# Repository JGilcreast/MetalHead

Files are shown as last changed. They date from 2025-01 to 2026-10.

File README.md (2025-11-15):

MetalHead

An opensource firmware and software drop-in replacement for the 85V Automatic Stirrup Bender by CRS Specialties Inc.
...short story behind the name...

# System Block Diagram
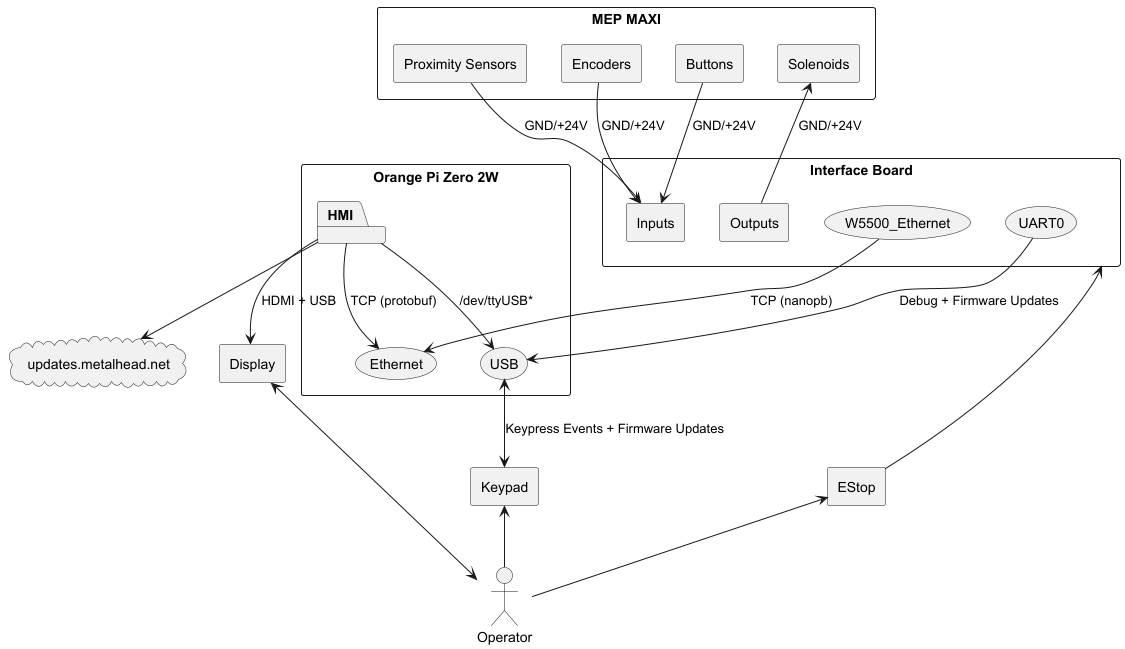
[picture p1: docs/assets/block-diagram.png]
Block Diagram


---

# Firmware
### HMI - Zephyr RTOS
* It's preferred to use CLion, 
* [Download](https://apps.microsoft.com/search?query=python&hl=en-US&gl=US) and install the latest version of python
* Install wget and 7Zip so that they're accessible via cmd:
  * `choco install wget 7zip`
* Verify python is accessible via cmd:
  * `python -V`
* Create python virtual environment
  * `cd MetalHead\firmware\interface-board-zephyr`
  * `python -m venv .\.venv`
* Enter python virtual environment
  * `.\.venv\Scripts\activate.bat`
* Update pip (optional)
  * `python.exe -m pip install --upgrade pip`
* Install west
  * `pip install west`
* Initiate the Zephyr-RTOS project
  * `west init`
* Set BOARD to rpi-pico
  * `west config zephyr.board rpi_pico`
* Pull the latest commits from Zephyr's github
  * `west update`
* Export a Zephyr CMake package. This allows CMake to automatically load boilerplate code required for building Zephyr applications.
  * `west zephyr-export`
  * > See: Computer\HKEY_CURRENT_USER\Software\Kitware\CMake\Packages
* Install additional packages need by west
  * `west packages pip --install`
* Install the Zephyr SDK
  * `west sdk install`
* Create a folder for bossac: C:\Program Files (x86)\BOSSA
* Copy bossac.exe to C:\Program Files (x86)\BOSSA
* Add C:\Program Files (x86)\BOSSA to PATH environment (use `sysdm.cpl`)
  * Make sure you can access bossac.exe. Open a new terminal and run: `bossac --help`
* Copy bossac.py from `MetalHead\firmware\interface-board-zephyr` to `MetalHead\firmware\interface-board-zephyr\zephyr\scripts\west_commands\runners`
* Start CLion
* Open our project: MetalHead\firmware\interface-board-zephyr\application
* Configure python interpreter for west
  * Go to File -> Settings -> Languages & Frameworks -> Python
  * Select the python interpreter from the list

To build a pristine copy of the firmware binary:[.gitignore](.gitignore)

  * `cd MetalHead\firmware\interface-board-zephyr`
  * `rmdir /q /s application\build`
  * Go back to CLion and reload West
  * Build, flash, etc

---

# Software
### HMI - Crude Edition
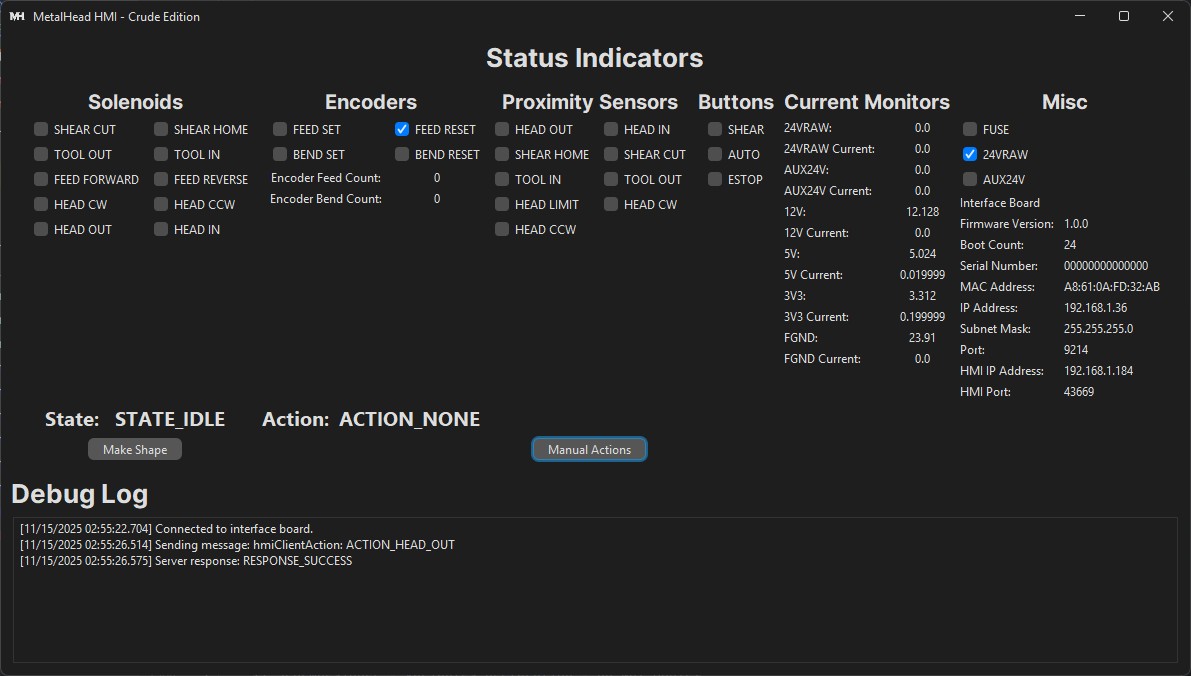
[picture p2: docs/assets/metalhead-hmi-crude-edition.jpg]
MetalHead HMI Crude Edition


This is a simple unpolished version of the HMI app that will eventually run on the orange pi.
This version is mostly for implementation and testing purposes.
### HMI
The polished version of the HMI app. This app version be able to accomplish the following:
* Must be able to communicate with the interface board bi-directionally
* Display all relevant information in realtime.
* Recognize user input from the custom keypad
* Offer simple 'wizards' that visually guide operators to make common shapes

Nice to have features:
* Auto-update HMI software by communicating to a remote server
* Auto-update interface firmware by communicating to a remote server
* Include a section for custom stirrup calculators/guides
* Include instructional videos on using the machinery

---

# Hardware
### Interface Board
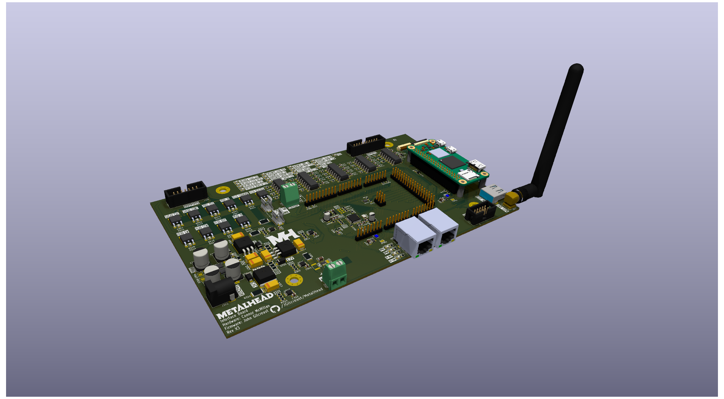
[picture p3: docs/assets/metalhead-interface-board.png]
MetalHead Interface Board


### Keypad
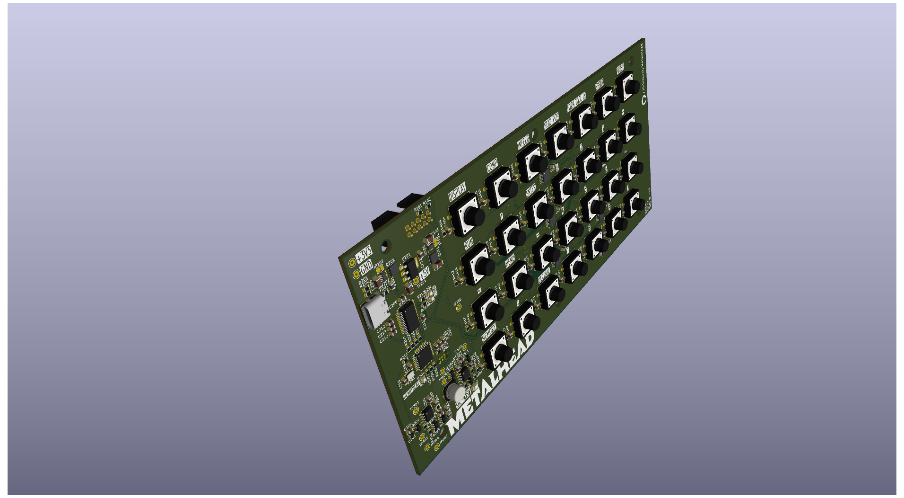
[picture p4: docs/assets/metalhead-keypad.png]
MetalHead Keypad


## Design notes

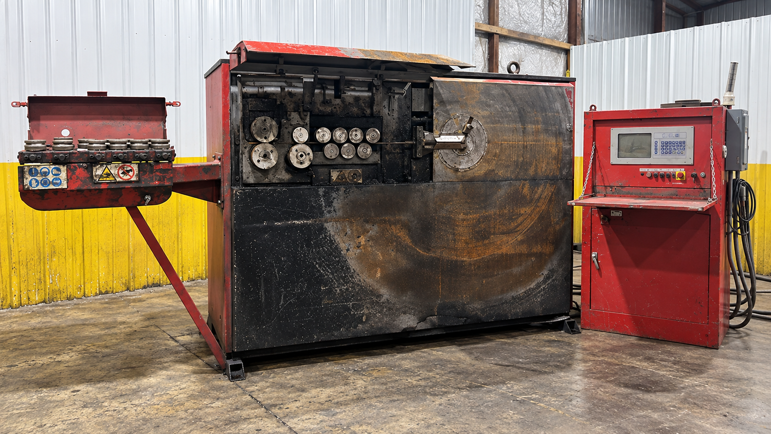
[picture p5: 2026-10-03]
docs/assets/CRS Specialties MEP MAXI 85V.png

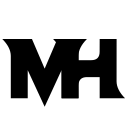
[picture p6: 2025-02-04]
docs/assets/MH-128.png

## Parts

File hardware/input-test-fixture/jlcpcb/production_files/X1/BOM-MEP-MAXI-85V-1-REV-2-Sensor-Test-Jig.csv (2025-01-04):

Comment | Designator | Footprint | LCSC | Quantity
Screw_Terminal_01x03 | J105 | TerminalBlock_TE_282834-3_1x03_P2.54mm_Horizontal |  | 1
Screw_Terminal_01x03 | J107 | TerminalBlock_TE_282834-3_1x03_P2.54mm_Horizontal |  | 1
Screw_Terminal_01x02 | J114 | TerminalBlock_TE_282834-2_1x02_P2.54mm_Horizontal |  | 1
Screw_Terminal_01x03 | J111 | TerminalBlock_TE_282834-3_1x03_P2.54mm_Horizontal |  | 1
Screw_Terminal_01x02 | J110 | TerminalBlock_TE_282834-2_1x02_P2.54mm_Horizontal |  | 1
Screw_Terminal_01x03 | J109 | TerminalBlock_TE_282834-3_1x03_P2.54mm_Horizontal |  | 1
Screw_Terminal_01x05 | J103 | TerminalBlock_TE_282834-5_1x05_P2.54mm_Horizontal |  | 1
Screw_Terminal_01x03 | J112 | TerminalBlock_TE_282834-3_1x03_P2.54mm_Horizontal |  | 1
Barrel_Jack_MountingPin | J115 | BarrelJack_Wuerth_6941xx301002 |  | 1
Conn_02x10_Odd_Even | J101 | IDC-Header_2x10_P2.54mm_Vertical |  | 1
Screw_Terminal_01x03 | J108 | TerminalBlock_TE_282834-3_1x03_P2.54mm_Horizontal |  | 1
Screw_Terminal_01x05 | J102 | TerminalBlock_TE_282834-5_1x05_P2.54mm_Horizontal |  | 1
Screw_Terminal_01x03 | J104 | TerminalBlock_TE_282834-3_1x03_P2.54mm_Horizontal |  | 1
Screw_Terminal_01x03 | J113 | TerminalBlock_TE_282834-3_1x03_P2.54mm_Horizontal |  | 1
Screw_Terminal_01x03 | J106 | TerminalBlock_TE_282834-3_1x03_P2.54mm_Horizontal |  | 1

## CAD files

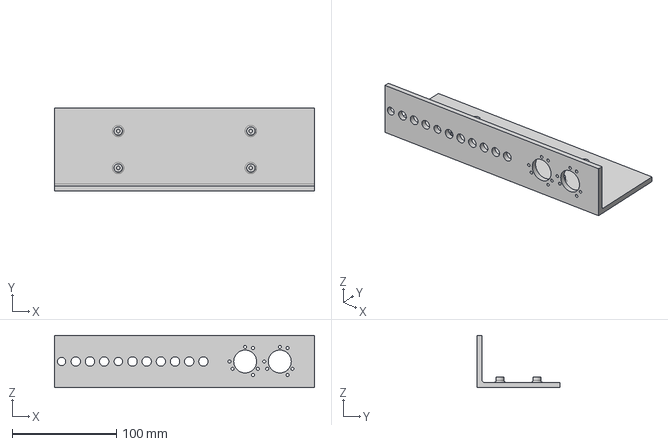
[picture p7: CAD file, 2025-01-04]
hardware/input-test-fixture/3D/X1/Input Test Fixture v3.step
250.0 x 80.0 x 50.0 mm

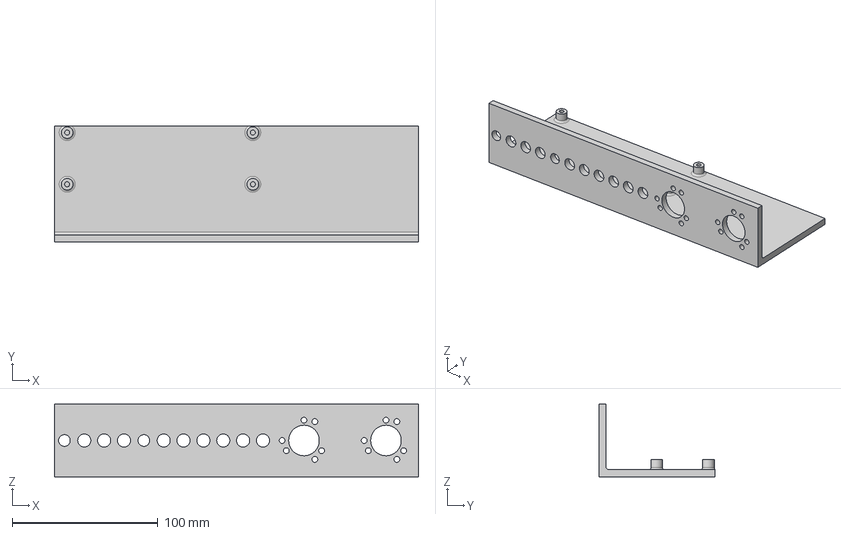
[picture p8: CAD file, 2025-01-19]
hardware/input-test-fixture/3D/X2/Input Test Fixture X2.step
250.0 x 80.0 x 50.0 mm

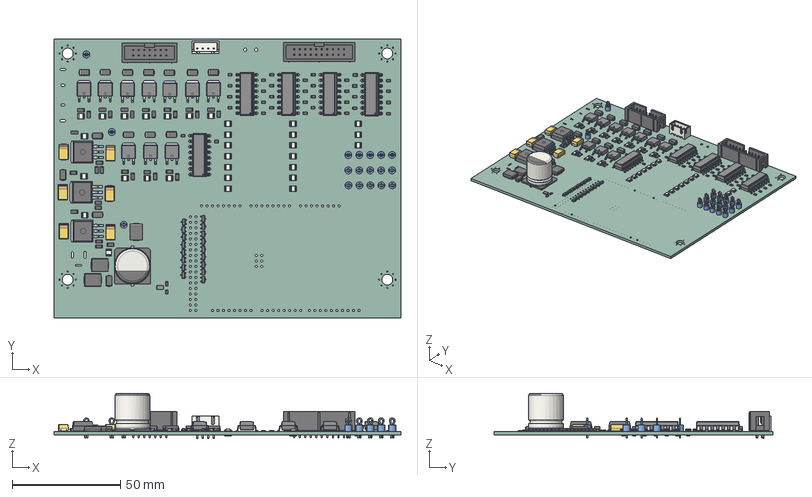
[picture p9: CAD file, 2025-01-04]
hardware/interface-board/production/X1/3D/MEP-MAXI-85V-1-REV-2-Interface-Board.step
160.0 x 128.5 x 20.9 mm
LED_1210_3225Metric x 31
D_SMA x 14
R_1206_3216Metric x 48
R_0805_2012Metric x 36
JST_B4B_XH_A
TestPoint_Loop_D2_60mm_Drill1_6mm_Beaded_cp x 18
SOT_23 x 17
IRFR7540TRPBF x 10
CP_EIA_7343_31_Kemet_D x 6
D_SMC x 3
LTV-846S x 5
CQ assembly x 3
CP_Elec_16x175
IDC_Header_2x10_P254mm_Vertical
ASSEMBLY
IDC_Header_2x07_P254mm_Vertical
_autosave-MEP-MAXI-85V-1-REV-2-Interface-Board_PCB

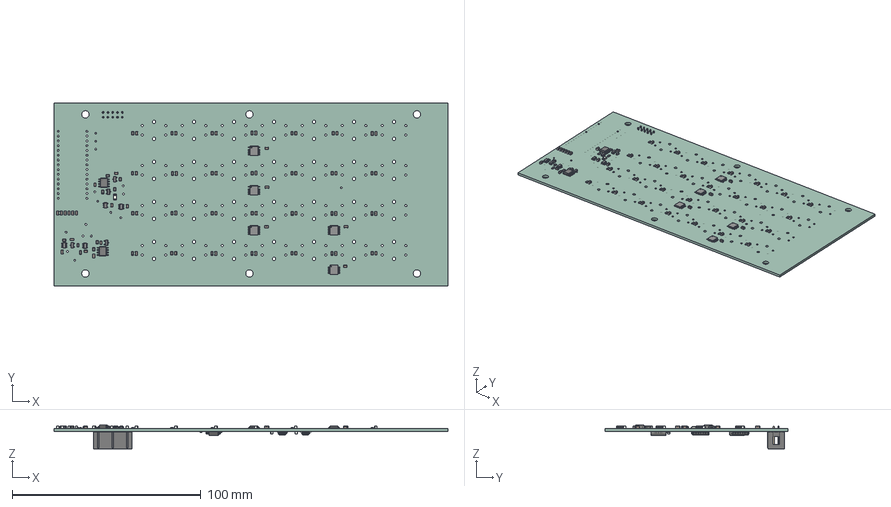
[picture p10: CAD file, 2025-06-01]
hardware/keypad/production/X1/3D/keypad.step
209.0 x 97.3 x 12.5 mm
C_0805_2012Metric x 55
R_0805_2012Metric x 43
SOIC-8_3.9x4.9mm_P1.27mm x 2
SOT-23 x 4
SN74LVC2G14DBVR x 4
SN74HC14PWR x 5
SC-74A-5_1.55x2.9mm_P0.95mm
LED_1206_3216Metric
SSOP-24_5.3x8.2mm_P0.65mm x 2
BODY-SO x 3
LEAD-SO x 42
PIN1-ID x 3
SOT-353_SC-70-5
IDC-Header_2x05_P2.54mm_Vertical
keypad_PCB

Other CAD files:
hardware/input-test-fixture/3D/X1/Input Test Fixture v3.iges
hardware/input-test-fixture/3D/X1/Input Test Fixture v3.stl

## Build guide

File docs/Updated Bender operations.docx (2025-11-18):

Typical Bender operation – Normal mode
Creating multiple pieces of a shape with N lines,

1) Shear and start [Full Re-home procedure]
  a) Reset head angle – [Return the head to default CW home position, either for CCW or CW bending]
    i) Determine if the next angle is cw or ccw bend
      (1) CW bends [Pin above rebar] – HEAD_CCW to trip proximity_head_cw
      (2) CCW bends [Pin below rebar] - HEAD_CW to trip proximity_head_ccw
    ii) How can we detect ‘limbo’? [What if head is past sensors on either side?]
      (1) PROXIMITY_HEAD_LIMIT sensor is likely at the edge of both halves of the head
      (2) If PROXIMITY_HEAD_LIMIT is tripped, reverse rotation until you hit the proper proximity sensor
      (3) Ex: For CW bends, if PROXIMITY_HEAD_LIMIT is tripped and HEAD_CCW is high, then change to HEAD_CW until proximity_head_cw is tripped
  b) Retract head & forming tool
    i) HEAD_IN to trip PROXIMITY_HEAD_IN
    ii) TOOL_IN to trip PROXIMITY_TOOL_IN
  c) Home shear and cut once to reset material
    i) SHEAR_HOME until PROXIMITY_SHEAR_HOME trips
    ii) SHEAR_CUT until PROXIMITY_SHEAR_CUT trips
    iii) SHEAR_HOME until PROXIMITY_SHEAR_HOME trips
  d) Extend head/forming tool until interrupt
    i) TOOL_OUT to trip PROXIMITY_TOOL_OUT
    ii) HEAD_OUT to trip PROXIMITY_HEAD_OUT
  e) Feed ‘X’ length. [Feed the material so that it reaches a pre-defined length, at the end of the forming tool]
    i) FEED_FORWARD until encoder_feed_set/_reset reaches ‘X’
      (1) Original machine uses both _set/_reset, ‘OR’ together. _reset is likely incremented by reverse movement
2) Lines x N

[Assuming continuous operation. Any pauses require a full re-home, repeat step 1 above.]

  a) Angle
    i) Check if next line cw or ccw, and set head angle to proper position¹
      (1) CW bends [Pin above rebar] – if proximity_head_ccw is tripped, retract head, head_ccw to trip proximity head cw, and extend head
      (2) CCW bends [Pin below rebar] – If proximity_head_ccw is tripped, retract head, HEAD_CW to trip proximity_head_ccw, and extend head
  b) Feed
    i) While materialFed < length*, feed
    ii) Every feed counter interrupt goes to previous step, increment on every interrupt
    iii) When materialFed >= length, move to bend
  c) Bend
    i) While materialBent < bend**, bend
    ii) Every bend counter interrupt goes to previous step, increment on every interrupt
    iii) When materialBent >= bend, unbend to reset
      (1) Count on interrupt to tell us the starting position, or do we need a counter?
  d) Repeat step 2 N times, once for each line
3) Finish the shape
  a) Retract head/tool
    i) HEAD_IN to trip PROXIMITY_HEAD_IN
    ii) TOOL_IN to trip PROXIMITY_TOOL_IN
  b) Retract rebar ‘X’ length, standardized to bring correct length from shear
    i) Should be roughly the same ‘x’ as in step 1.e
  c) Cut shape
    i) SHEAR_HOME until PROXIMITY_SHEAR_HOME trips [Limbo check]
    ii) SHEAR_CUT until PROXIMITY_SHEAR_CUT trips
    iii) SHEAR_HOME until PROXIMITY_SHEAR_HOME trips
  d) Extend head/forming tool until interrupt
    i) TOOL_OUT to trip PROXIMITY_TOOL_OUT
    ii) HEAD_OUT to trip PROXIMITY_HEAD_OUT
  e) Increment runCount, return to Step 2 if runCount <= totalPieces

# Notes

- Re-start
  - If the machine has been stopped in the middle of a run, a full re-home is required
- 2 types of re-home
  - A full re-home is required at the start of a run, or resuming after a pause
    - Full ‘limbo’ checking
  - A mid-run re-home is required after every continuous shape is cut in a run
    - Because the machine is already running automatically, we can assume that the shear is home and that the head/tool in/out are home. Head angle will have to be checked, because each angle can be cw or ccw

¹ – We can assume the head angle is at one of the sensor positions because the machine would be continuously running. Any pause requires a re-home operation.

*Length formula: (length + lengthCompensation) * feedScale * barSizeModifier
**Bend formula: (bend + bendCompensation) * centerPinModifier (?) barBendModifier

length = length programmed per line
lengthCompensation = compensation programmed per line
feedScale = systemwide modifier, programmed from settings
barSizeModifier = system adjustment for different sizes of rebar (4/8” vs 5/8”, etc)
bend = bend programmed per line

bendCompensation = bend compensation programmed per line

centerPinModifier = bend compensation for different center pin sizes

barBendModifier = bend compensation for different sizes of rebar

HMI logic -
mid-run pause leads to two options ‘remake shape’ and ‘continue’. Remake shape does a full re-home, cutting any half-finished material immediately. Continue keeps going from where the run left off, at operator’s risk.

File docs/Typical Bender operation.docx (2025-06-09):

Typical Bender operation – Normal mode
Creating multiple pieces of a shape with N lines,

1) Shear and start
  a) Reset head angle
  b) Retract head/forming tool until interrupt
  c) Shear Extend until sensor interrupt / shear Retract until sensor interrupt
  d) Extend head/forming tool until interrupt
  e) Feed ‘X’ length, standardized to move past center pin
2) Lines x N
  a) Feed
    i) While materialFed < length*, feed
    ii) Every feed counter interrupt goes to previous step, increment on every interrupt
    iii) When materialFed >= length, move to bend
  b) Bend
    i) While materialBent < bend**, bend
    ii) Every bend counter interrupt goes to previous step, increment on every interrupt
    iii) When materialBent >= bend, unbend to reset
      (1) Count on interrupt to tell us the starting position, or do we need a counter?
  c) Repeat step 2 N times, once for each line
3) Finish
  a) Retract
    i) Retract head/forming tool
    ii) Retract rebar ‘X’ length, standardized to bring correct length from shear
  b) Cut
    i) Shear Extend until sensor interrupt / Shear Retract until sensor interrupt
    ii) Extend head/forming tool until interrupt
    iii) Reset head angle
    iv) Feed ‘X’ length, standardized to move past center pin
    v) Increment runCount, return to Step 2 if runCount <= totalPieces

*Length formula: (length + lengthCompensation) * feedScale * barSizeModifier
**Bend formula: (bend + bendCompensation) * centerPinModifier (?) barBendModifier

length = length programmed per line
lengthCompensation = compensation programmed per line
feedScale = systemwide modifier, programmed from settings
barSizeModifier = system adjustment for different sizes of rebar (4/8” vs 5/8”, etc)
bend = bend programmed per line

bendCompensation = bend compensation programmed per line

centerPinModifier = bend compensation for different center pin sizes

barBendModifier = bend compensation for different sizes of rebar

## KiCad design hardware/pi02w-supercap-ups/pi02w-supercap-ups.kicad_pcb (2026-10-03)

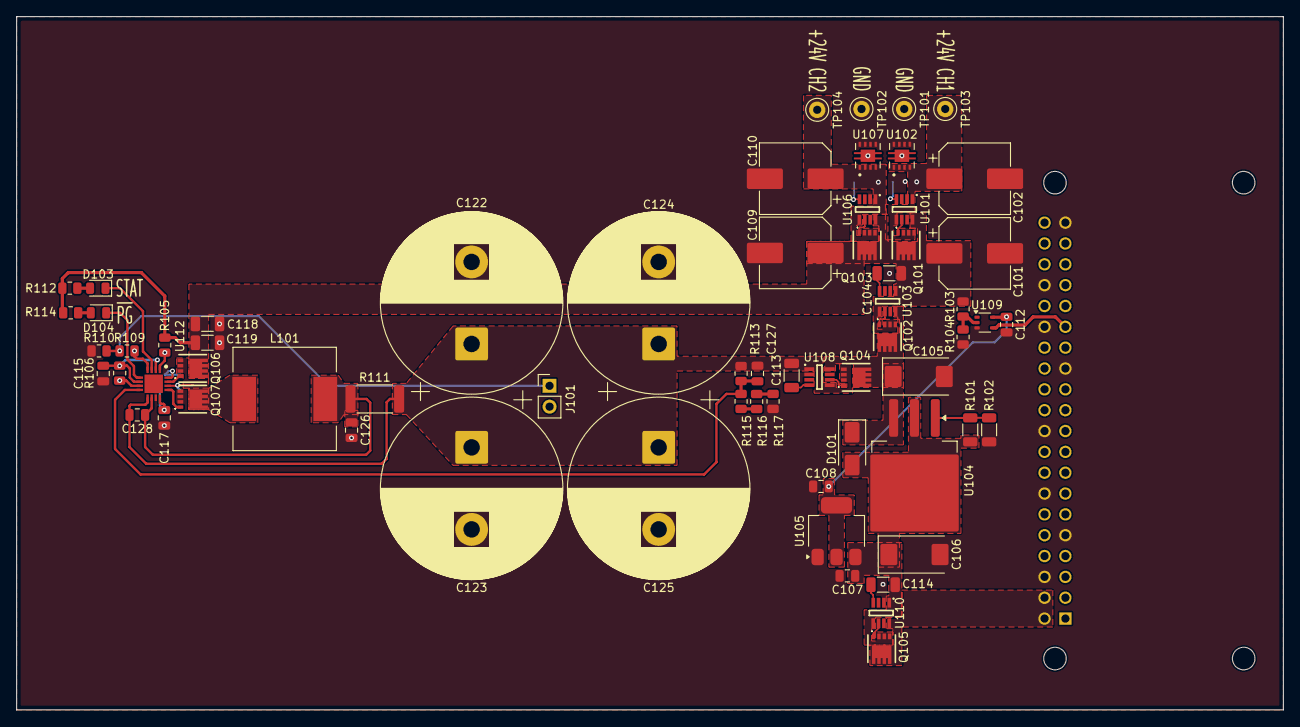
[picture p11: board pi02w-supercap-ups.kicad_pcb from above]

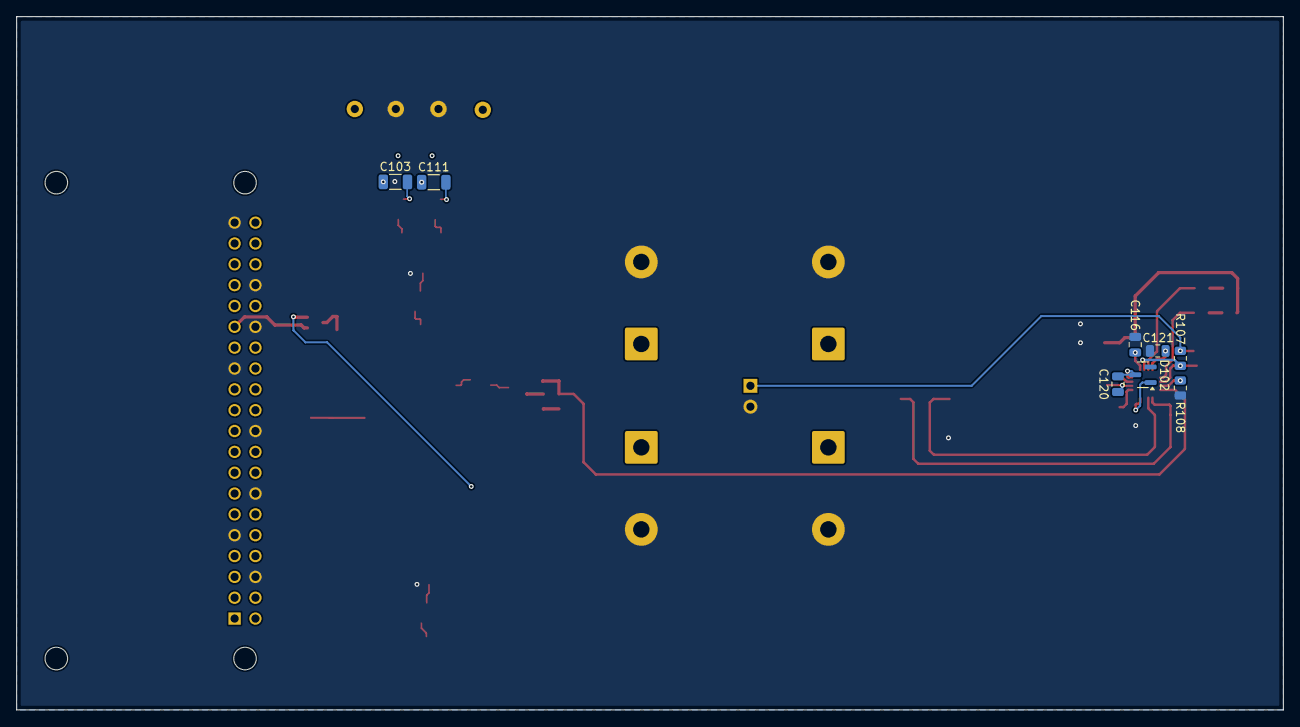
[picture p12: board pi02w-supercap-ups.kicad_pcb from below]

Board: 2 copper layers, 154.4 x 84.5 mm, 74 parts (8 on the bottom side), 40 nets.

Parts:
C101, C102, C109, C110: 330uF 25V; CP_Elec_8x10.5
C103, C104, C111, C113, C114: 100nF; C_1206_3216Metric
C105, C106: 10uF 50V; CP_EIA-7343-31_Kemet-D
C107, C108: 100nF; C_0805_2012Metric
C112, C115, C116, C117: 1uF; C_0805_2012Metric
C118, C119: 10uF; C_1206_3216Metric
C120, C121, C126, C128: 0.1uF; C_0805_2012Metric
C122, C123, C124, C125: 22000uF/25V; CP_Radial_D22.0mm_P10.00mm_SnapIn
C127: 22pF; C_0805_2012Metric
D101: 1N4002 M2; D_SMA
D102: BAT54C; SOT-23
D103: RED; LED_0805_2012Metric
D104: GREEN; LED_0805_2012Metric
J101: SEMITEC 103AT-2; PinHeader_1x02_P2.54mm_Vertical
L101: 10uH; L_12x12mm_H8mm
Q101, Q102, Q103, Q104, Q105, Q106, Q107: DMT6007LFG; DMP4013LFG7
R101: 300R; R_1206_3216Metric
R102: 900R; R_1206_3216Metric
R103: 62K; R_0805_2012Metric
R104: 10K; R_0805_2012Metric
R105: 10R; R_0805_2012Metric
R106: 100K; R_0805_2012Metric
R107: 9.31K; R_0805_2012Metric
R108: 22.1K; R_0805_2012Metric
R109: 100R; R_0805_2012Metric
R110: 430K; R_0805_2012Metric
R111: 10mR; R_2512_6332Metric
R112, R114: 2K2; R_0805_2012Metric
R113: 5K1; R_0805_2012Metric
R115: 430R; R_0805_2012Metric
R116: 56R; R_0805_2012Metric
R117: 3R; R_0805_2012Metric
TP101, TP102: 125-00869; TestPoint_Keystone_5000-5004_Miniature
TP103, TP104: 125-00868; TestPoint_Keystone_5000-5004_Miniature
U101, U103, U106, U108, U110: LM74700QDDFRQ1; SOT65P280X110-8N
U102, U107: TVS2701DRBR; IC_TVS2701DRBR
U104: LM1084-ADJ; TO-263-3_TabPin2
U105: AMS1117-3.3; SOT-223-3_TabPin2
U109: 74LVC1G14GW-Q100,1; SOT-353_SC-70-5
U111: RASPBERRY_PI_ZERO_2_W; MODULE_RASPBERRY_PI_ZERO_2_W
U112: BQ24640RVAR; QFN50P350X350X100-17N-D

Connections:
24VCC: C105.1, D101.1 (K), Q102.2 (D), Q104.2 (D), U103.8 (CATHODE), U104.3 (VI), U108.8 (CATHODE)
+3V3: C108.1, C112.1, U105.2 (VO), U109.5 (VCC)
+5V: C106.1, C107.1, C114.1, D101.2 (A), Q105.3 (S), R101.1, U104.2 (VO), U105.3 (VI), U110.1 (EN), U110.5 (ANODE)
+24V: C101.1, C104.1, C109.1, C118.1, C119.1, Q101.2 (D), Q102.3 (S), Q103.2 (D), Q106.2 (D), R103.1, R105.1, R112.1, R114.1, U101.8 (CATHODE), U103.1 (EN), U103.5 (ANODE), U106.8 (CATHODE)
/24VGATE: R103.2, R104.1, U109.2
/BTST: C120.1, D102.3 (K), U112.16 (BTST)
/HIDRV: Q106.1 (G), U112.15 (HIDRV)
/ISET: R106.2, R108.1, U112.7 (ISET)
/LODRV: Q107.1 (G), U112.13 (LODRV)
/PH: C120.2, L101.1, Q106.3 (S), Q107.2 (D), U112.14 (PH)
/PI02W5VCC: Q105.2 (D), U110.8 (CATHODE), U111.2 (5V_2), U111.4 (5V_4)
/PWRSNS: U109.4, U111.29 (GPIO5)
/REGN: C117.1, D102.1 (A), U112.12 (REGN)
/SRP: C126.2, C128.1, L101.2, R111.1, U112.10 (SRP)
/STAT: D103.1 (K), U112.3 (STAT)
/THERM: J101.1, R107.2, R109.1, R110.1
/TS: C121.1, R109.2, U112.4 (TS)
/VCC: C116.1, R105.2, U112.1 (VCC)
/VFB: C127.2, R113.2, R115.1, U112.8 (VFB)
/VREF: C115.1, R106.1, R107.1, U112.2 (CE), U112.6 (VREF)
/~PG: D104.1 (K), U112.5 (~PG)
GND: C101.2, C102.2, C105.2, C106.2, C107.2, C108.2, C109.2, C110.2, C112.2, C115.2, C116.2, C117.2, C118.2, C119.2, C121.2, C122.2, C123.2, C124.2, C125.2, C126.1, J101.2, Q107.3 (S), R102.2, R104.2, R108.2, R110.2, R117.2, TP101.1, TP102.1, U101.2 (GND), U102.5 (GND), U102.6 (GND), U102.7 (GND), U102.8 (GND), U103.2 (GND), U105.1 (GND), U106.2 (GND), U107.5 (GND), U107.6 (GND), U107.7 (GND), U107.8 (GND), U108.2 (GND), U109.3 (GND), U110.2 (GND), U111.6 (GND_6), U111.9 (GND_9), U111.14 (GND_14), U111.20 (GND_20), U111.25 (GND_25), U111.30 (GND_30), U111.34 (GND_34), U111.39 (GND_39), U112.11 (GND), U112.17 (EP)
unnamed: D103.2 (A), R112.2
unnamed: D104.2 (A), R114.2
unnamed: Q101.1 (G), U101.6 (GATE)
unnamed: Q102.1 (G), U103.6 (GATE)
unnamed: Q103.1 (G), U106.6 (GATE)
unnamed: Q104.1 (G), U108.6 (GATE)
unnamed: Q105.1 (G), U110.6 (GATE)
unnamed: R115.2, R116.1
unnamed: R116.2, R117.1
unnamed: C103.2, U101.4 (VCAP)
unnamed: C104.2, U103.4 (VCAP)
unnamed: R101.2, R102.1, U104.1 (ADJ)
unnamed: C111.2, U106.4 (VCAP)
unnamed: C113.2, U108.4 (VCAP)
unnamed: C114.2, U110.4 (VCAP)
RAW24V1: C102.1, C103.1, Q101.3 (S), TP103.1, U101.1 (EN), U101.5 (ANODE), U102.1 (IN), U102.2 (IN), U102.3 (IN), U102.4 (IN)
RAW24V2: C110.1, C111.1, Q103.3 (S), TP104.1, U106.1 (EN), U106.5 (ANODE), U107.1 (IN), U107.2 (IN), U107.3 (IN), U107.4 (IN)
UPS24V: C113.1, C122.1, C123.1, C124.1, C125.1, C127.1, C128.2, Q104.3 (S), R111.2, R113.1, U108.1 (EN), U108.5 (ANODE), U112.9 (SRN)

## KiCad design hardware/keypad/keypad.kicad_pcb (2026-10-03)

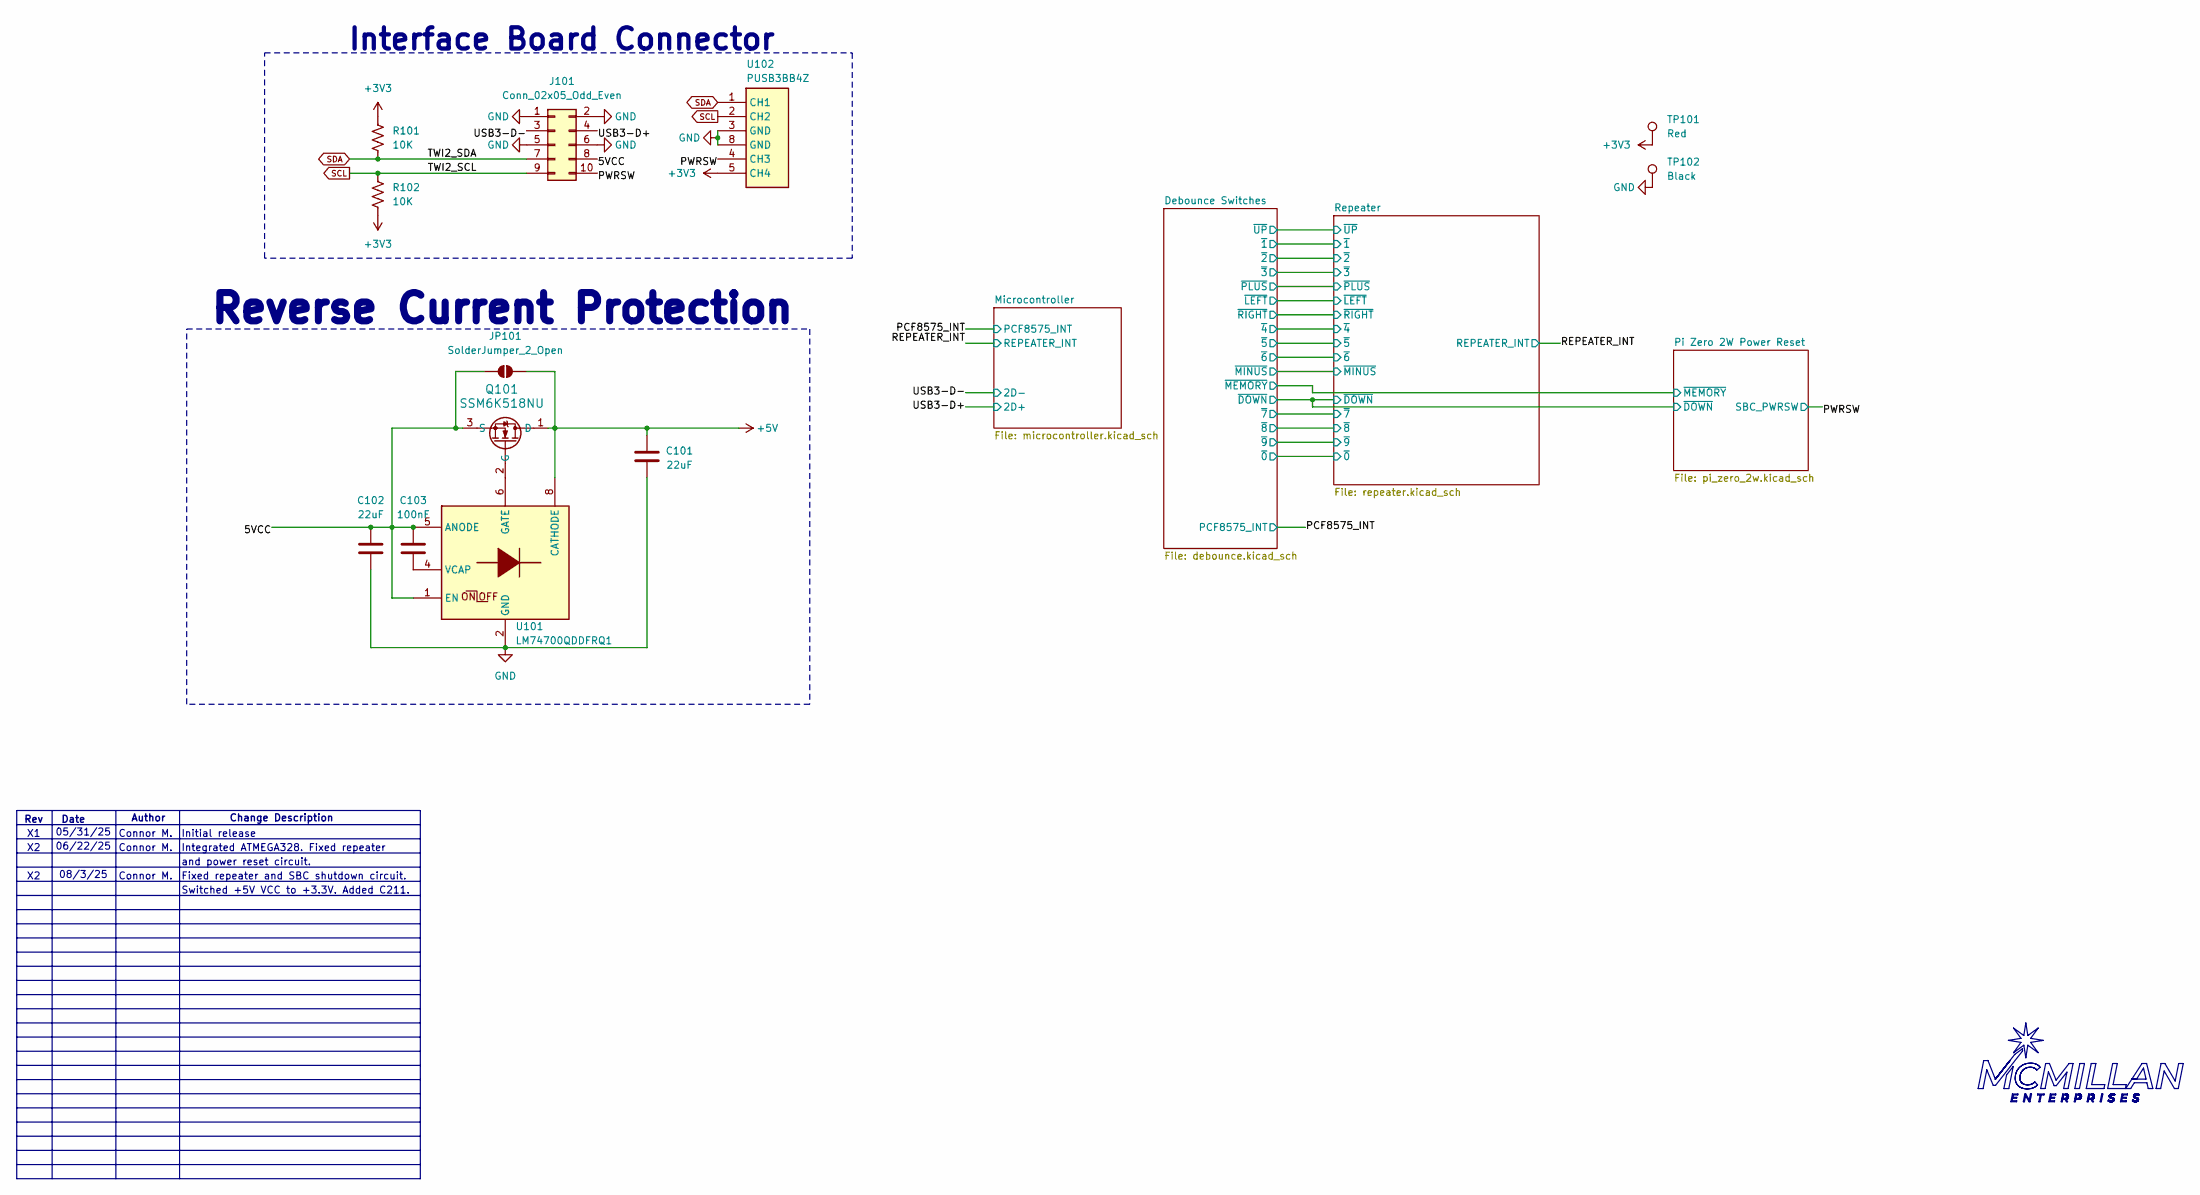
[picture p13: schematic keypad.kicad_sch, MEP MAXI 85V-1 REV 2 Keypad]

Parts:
C101, C102: 22uF; C_1206_3216Metric
C103: 100nF; C_1206_3216Metric
J101: Conn_02x05_Odd_Even; IDC-Header_2x05_P2.54mm_Vertical
JP101: SolderJumper_2_Open; SolderJumper-2_P1.3mm_Open_TrianglePad1.0x1.5mm
Q101: SSM6K518NU; SOT-1220UDFN6B_TOS
R101, R102: 10K; R_0805_2012Metric
TP101: Red; TestPoint_Keystone_5000-5004_Miniature
TP102: Black; TestPoint_Keystone_5000-5004_Miniature
U101: LM74700QDDFRQ1; SOT65P280X110-8N; Mouser Part Number 595-LM74700QDDFRQ1
U102: PUSB3BB4Z; SON50P100X250X50-10N; Mouser Part Number 771-PUSB3BB4Z

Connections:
+3V3: R101.1, R102.2, TP101.1, U102.5 (CH4); also elsewhere on the board
/5VCC: C102.1, C103.1, J101.8, JP101.1 (A), Q101.3 (S), U101.1 (EN), U101.5 (ANODE)
/PWRSW: J101.10, U102.4 (CH3); also elsewhere on the board
/USB3-D+: J101.4; also elsewhere on the board
/USB3-D-: J101.3; also elsewhere on the board
GND: C101.2, C102.2, J101.1, J101.2, J101.5, J101.6, TP102.1, U101.2 (GND), U102.3 (GND), U102.8 (GND); also elsewhere on the board
unnamed: C103.2, U101.4 (VCAP)
SCL: J101.9, R102.1, U102.2 (CH2); also elsewhere on the board
SDA: J101.7, R101.2, U102.1 (CH1); also elsewhere on the board

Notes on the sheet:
Change Description
Interface Board Connector
Integrated ATMEGA328. Fixed repeater
Date
Connor M.
and power reset circuit.
Initial release
Switched +5V VCC to +3.3V. Added C211.
08/3/25
Author
06/22/25
Reverse Current Protection
Fixed repeater and SBC shutdown circuit.
Rev
05/31/25

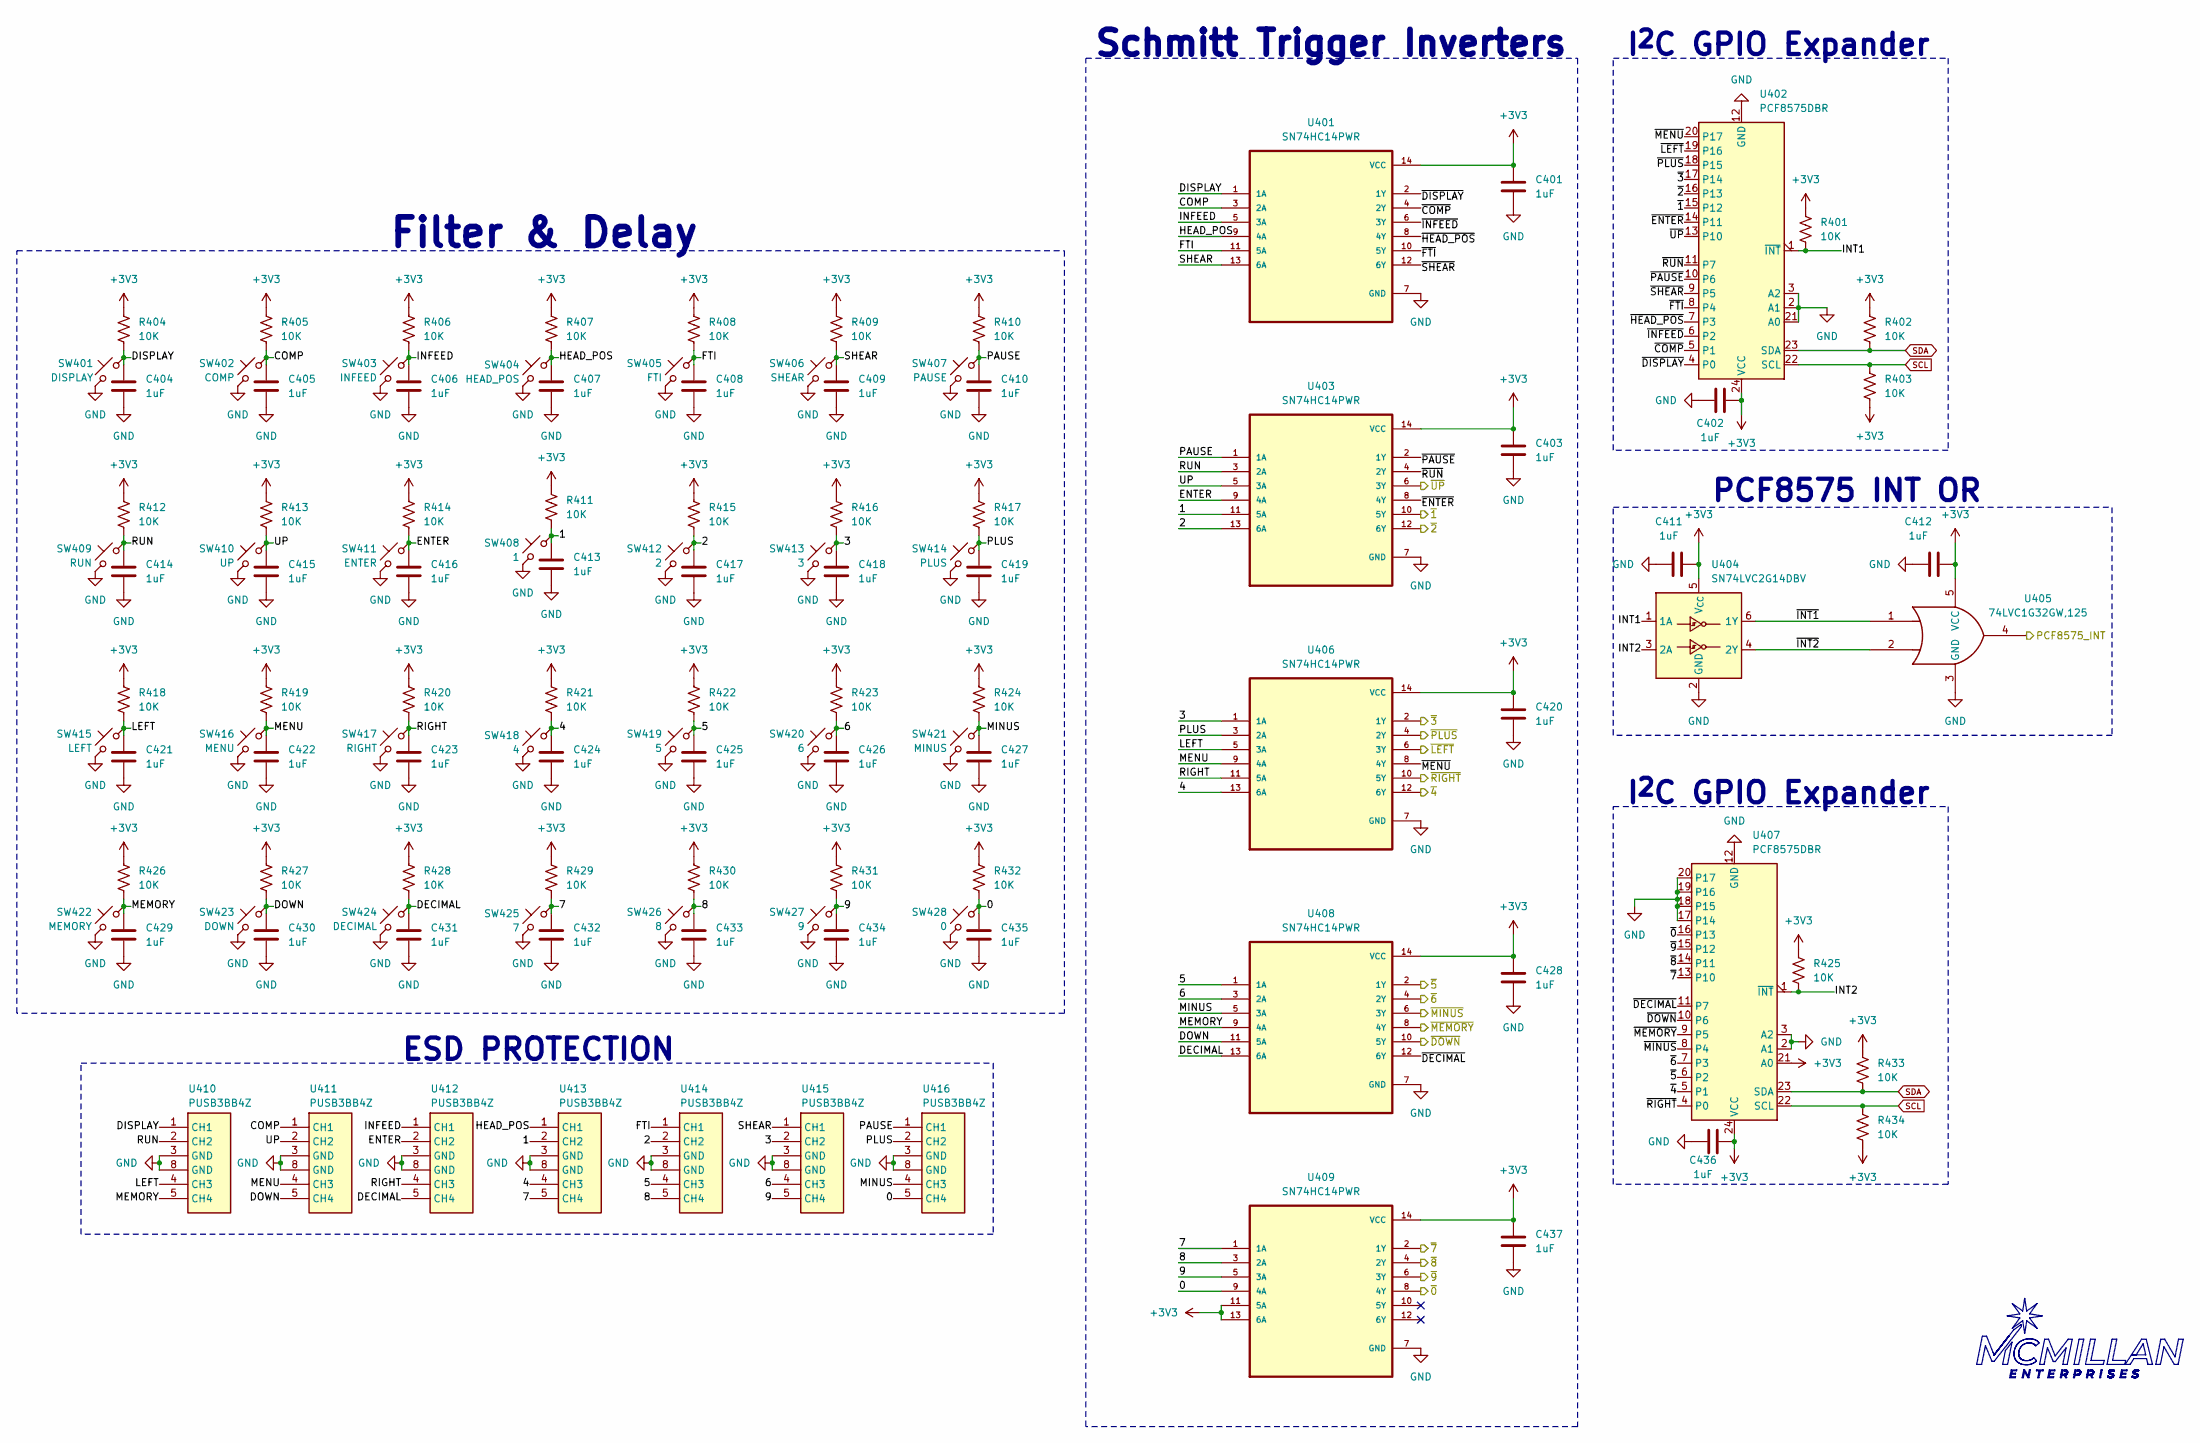
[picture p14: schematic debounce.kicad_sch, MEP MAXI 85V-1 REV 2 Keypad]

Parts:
C401, C402, C403, C404, C405, C406, C407, C408, C409, C410, C411, C412, C413, C414, C415, C416, C417, C418, C419, C420, C421, C422, C423, C424, C425, C426, C427, C428, C429, C430, C431, C432, C433, C434, C435, C436, C437: 1uF; C_0805_2012Metric
R401, R402, R403, R404, R405, R406, R407, R408, R409, R410, R411, R412, R413, R414, R415, R416, R417, R418, R419, R420, R421, R422, R423, R424, R425, R426, R427, R428, R429, R430, R431, R432, R433, R434: 10K; R_0805_2012Metric
SW401: DISPLAY; SW_SPST_Omron_B3F-40xx
SW402: COMP; SW_SPST_Omron_B3F-40xx
SW403: INFEED; SW_SPST_Omron_B3F-40xx
SW404: HEAD_POS; SW_SPST_Omron_B3F-40xx
SW405: FTI; SW_SPST_Omron_B3F-40xx
SW406: SHEAR; SW_SPST_Omron_B3F-40xx
SW407: PAUSE; SW_SPST_Omron_B3F-40xx
SW408: 1; SW_SPST_Omron_B3F-40xx
SW409: RUN; SW_SPST_Omron_B3F-40xx
SW410: UP; SW_SPST_Omron_B3F-40xx
SW411: ENTER; SW_SPST_Omron_B3F-40xx
SW412: 2; SW_SPST_Omron_B3F-40xx
SW413: 3; SW_SPST_Omron_B3F-40xx
SW414: PLUS; SW_SPST_Omron_B3F-40xx
SW415: LEFT; SW_SPST_Omron_B3F-40xx
SW416: MENU; SW_SPST_Omron_B3F-40xx
SW417: RIGHT; SW_SPST_Omron_B3F-40xx
SW418: 4; SW_SPST_Omron_B3F-40xx
SW419: 5; SW_SPST_Omron_B3F-40xx
SW420: 6; SW_SPST_Omron_B3F-40xx
SW421: MINUS; SW_SPST_Omron_B3F-40xx
SW422: MEMORY; SW_SPST_Omron_B3F-40xx
SW423: DOWN; SW_SPST_Omron_B3F-40xx
SW424: DECIMAL; SW_SPST_Omron_B3F-40xx
SW425: 7; SW_SPST_Omron_B3F-40xx
SW426: 8; SW_SPST_Omron_B3F-40xx
SW427: 9; SW_SPST_Omron_B3F-40xx
SW428: 0; SW_SPST_Omron_B3F-40xx
U401, U403, U406, U408, U409: SN74HC14PWR; SOP65P640X120-14N
U402, U407: PCF8575DBR; SSOP-24_5.3x8.2mm_P0.65mm
U404: SN74LVC2G14DBV; SOT95P280X145-6N
U405: 74LVC1G32GW,125; SOT-353_SC-70-5
U410, U411, U412, U413, U414, U415, U416: PUSB3BB4Z; SON50P100X250X50-10N; Mouser Part Number 771-PUSB3BB4Z

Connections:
+3V3: C401.1, C402.2, C403.1, C411.2, C412.2, C420.1, C428.1, C436.2, C437.1, R401.1, R402.1, R403.2, R404.1, R405.1, R406.1, R407.1, R408.1, R409.1, R410.1, R411.1, R412.1, R413.1, R414.1, R415.1, R416.1, R417.1, R418.1, R419.1, R420.1, R421.1, R422.1, R423.1, R424.1, R425.1, R426.1, R427.1, R428.1, R429.1, R430.1, R431.1, R432.1, R433.1, R434.2, U401.14 (VCC), U402.24 (VCC), U403.14 (VCC), U404.5 (V_{CC}), U405.5 (VCC), U406.14 (VCC), U407.21 (A0), U407.24 (VCC), U408.14 (VCC), U409.11 (5A), U409.13 (6A), U409.14 (VCC); also elsewhere on the board
/Debounce Switches/0: C435.1, R432.2, SW428.2, U409.9 (4A), U416.5 (CH4)
/Debounce Switches/1: C413.1, R411.2, SW408.2, U403.11 (5A), U413.2 (CH2)
/Debounce Switches/2: C417.1, R415.2, SW412.2, U403.13 (6A), U414.2 (CH2)
/Debounce Switches/3: C418.1, R416.2, SW413.2, U406.1 (1A), U415.2 (CH2)
/Debounce Switches/4: C424.1, R421.2, SW418.2, U406.13 (6A), U413.4 (CH3)
/Debounce Switches/5: C425.1, R422.2, SW419.2, U408.1 (1A), U414.4 (CH3)
/Debounce Switches/6: C426.1, R423.2, SW420.2, U408.3 (2A), U415.4 (CH3)
/Debounce Switches/7: C432.1, R429.2, SW425.2, U409.1 (1A), U413.5 (CH4)
/Debounce Switches/8: C433.1, R430.2, SW426.2, U409.3 (2A), U414.5 (CH4)
/Debounce Switches/9: C434.1, R431.2, SW427.2, U409.5 (3A), U415.5 (CH4)
/Debounce Switches/COMP: C405.1, R405.2, SW402.2, U401.3 (2A), U411.1 (CH1)
/Debounce Switches/DECIMAL: C431.1, R428.2, SW424.2, U408.13 (6A), U412.5 (CH4)
/Debounce Switches/DISPLAY: C404.1, R404.2, SW401.2, U401.1 (1A), U410.1 (CH1)
/Debounce Switches/DOWN: C430.1, R427.2, SW423.2, U408.11 (5A), U411.5 (CH4)
/Debounce Switches/ENTER: C416.1, R414.2, SW411.2, U403.9 (4A), U412.2 (CH2)
/Debounce Switches/FTI: C408.1, R408.2, SW405.2, U401.11 (5A), U414.1 (CH1)
/Debounce Switches/HEAD_POS: C407.1, R407.2, SW404.2, U401.9 (4A), U413.1 (CH1)
/Debounce Switches/INFEED: C406.1, R406.2, SW403.2, U401.5 (3A), U412.1 (CH1)
/Debounce Switches/INT1: R401.2, U402.1 (~INT), U404.1 (1A)
/Debounce Switches/INT2: R425.2, U404.3 (2A), U407.1 (~INT)
/Debounce Switches/LEFT: C421.1, R418.2, SW415.2, U406.5 (3A), U410.4 (CH3)
/Debounce Switches/MEMORY: C429.1, R426.2, SW422.2, U408.9 (4A), U410.5 (CH4)
/Debounce Switches/MENU: C422.1, R419.2, SW416.2, U406.9 (4A), U411.4 (CH3)
/Debounce Switches/MINUS: C427.1, R424.2, SW421.2, U408.5 (3A), U416.4 (CH3)
/Debounce Switches/PAUSE: C410.1, R410.2, SW407.2, U403.1 (1A), U416.1 (CH1)
/Debounce Switches/PLUS: C419.1, R417.2, SW414.2, U406.3 (2A), U416.2 (CH2)
/Debounce Switches/RIGHT: C423.1, R420.2, SW417.2, U406.11 (5A), U412.4 (CH3)
/Debounce Switches/RUN: C414.1, R412.2, SW409.2, U403.3 (2A), U410.2 (CH2)
/Debounce Switches/SHEAR: C409.1, R409.2, SW406.2, U401.13 (6A), U415.1 (CH1)
/Debounce Switches/UP: C415.1, R413.2, SW410.2, U403.5 (3A), U411.2 (CH2)
/Debounce Switches/~0: U407.16 (P13), U409.8 (4Y); also elsewhere on the board
/Debounce Switches/~1: U402.15 (P12), U403.10 (5Y); also elsewhere on the board
/Debounce Switches/~2: U402.16 (P13), U403.12 (6Y); also elsewhere on the board
/Debounce Switches/~3: U402.17 (P14), U406.2 (1Y); also elsewhere on the board
/Debounce Switches/~4: U406.12 (6Y), U407.5 (P1); also elsewhere on the board
/Debounce Switches/~5: U407.6 (P2), U408.2 (1Y); also elsewhere on the board
/Debounce Switches/~6: U407.7 (P3), U408.4 (2Y); also elsewhere on the board
/Debounce Switches/~7: U407.13 (P10), U409.2 (1Y); also elsewhere on the board
/Debounce Switches/~8: U407.14 (P11), U409.4 (2Y); also elsewhere on the board
/Debounce Switches/~9: U407.15 (P12), U409.6 (3Y); also elsewhere on the board
/Debounce Switches/~COMP: U401.4 (2Y), U402.5 (P1)
/Debounce Switches/~DECIMAL: U407.11 (P7), U408.12 (6Y)
/Debounce Switches/~DISPLAY: U401.2 (1Y), U402.4 (P0)
/Debounce Switches/~DOWN: U407.10 (P6), U408.10 (5Y); also elsewhere on the board
/Debounce Switches/~ENTER: U402.14 (P11), U403.8 (4Y)
/Debounce Switches/~FTI: U401.10 (5Y), U402.8 (P4)
/Debounce Switches/~HEAD_POS: U401.8 (4Y), U402.7 (P3)
/Debounce Switches/~INFEED: U401.6 (3Y), U402.6 (P2)
/Debounce Switches/~INT1: U404.6 (1Y), U405.1
/Debounce Switches/~INT2: U404.4 (2Y), U405.2
/Debounce Switches/~LEFT: U402.19 (P16), U406.6 (3Y); also elsewhere on the board
/Debounce Switches/~MEMORY: U407.9 (P5), U408.8 (4Y); also elsewhere on the board
/Debounce Switches/~MENU: U402.20 (P17), U406.8 (4Y)
/Debounce Switches/~MINUS: U407.8 (P4), U408.6 (3Y); also elsewhere on the board
/Debounce Switches/~PAUSE: U402.10 (P6), U403.2 (1Y)
/Debounce Switches/~PLUS: U402.18 (P15), U406.4 (2Y); also elsewhere on the board
/Debounce Switches/~RIGHT: U406.10 (5Y), U407.4 (P0); also elsewhere on the board
/Debounce Switches/~RUN: U402.11 (P7), U403.4 (2Y)
/Debounce Switches/~SHEAR: U401.12 (6Y), U402.9 (P5)
/Debounce Switches/~UP: U402.13 (P10), U403.6 (3Y); also elsewhere on the board
/PCF8575_INT: U405.4; also elsewhere on the board
GND: C401.2, C402.1, C403.2, C404.2, C405.2, C406.2, C407.2, C408.2, C409.2, C410.2, C411.1, C412.1, C413.2, C414.2, C415.2, C416.2, C417.2, C418.2, C419.2, C420.2, C421.2, C422.2, C423.2, C424.2, C425.2, C426.2, C427.2, C428.2, C429.2, C430.2, C431.2, C432.2, C433.2, C434.2, C435.2, C436.1, C437.2, SW401.1, SW402.1, SW403.1, SW404.1, SW405.1, SW406.1, SW407.1, SW408.1, SW409.1, SW410.1, SW411.1, SW412.1, SW413.1, SW414.1, SW415.1, SW416.1, SW417.1, SW418.1, SW419.1, SW420.1, SW421.1, SW422.1, SW423.1, SW424.1, SW425.1, SW426.1, SW427.1, SW428.1, U401.7 (GND), U402.2 (A1), U402.3 (A2), U402.12 (GND), U402.21 (A0), U403.7 (GND), U404.2 (GND), U405.3 (GND), U406.7 (GND), U407.2 (A1), U407.3 (A2), U407.12 (GND), U407.17 (P14), U407.18 (P15), U407.19 (P16), U407.20 (P17), U408.7 (GND), U409.7 (GND), U410.3 (GND), U410.8 (GND), U411.3 (GND), U411.8 (GND), U412.3 (GND), U412.8 (GND), U413.3 (GND), U413.8 (GND), U414.3 (GND), U414.8 (GND), U415.3 (GND), U415.8 (GND), U416.3 (GND), U416.8 (GND); also elsewhere on the board
SCL: R403.1, R434.1, U402.22 (SCL), U407.22 (SCL); also elsewhere on the board
SDA: R402.2, R433.2, U402.23 (SDA), U407.23 (SDA); also elsewhere on the board

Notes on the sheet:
I^{2}C GPIO Expander
Schmitt Trigger Inverters
PCF8575 INT OR
ESD PROTECTION
Filter & Delay

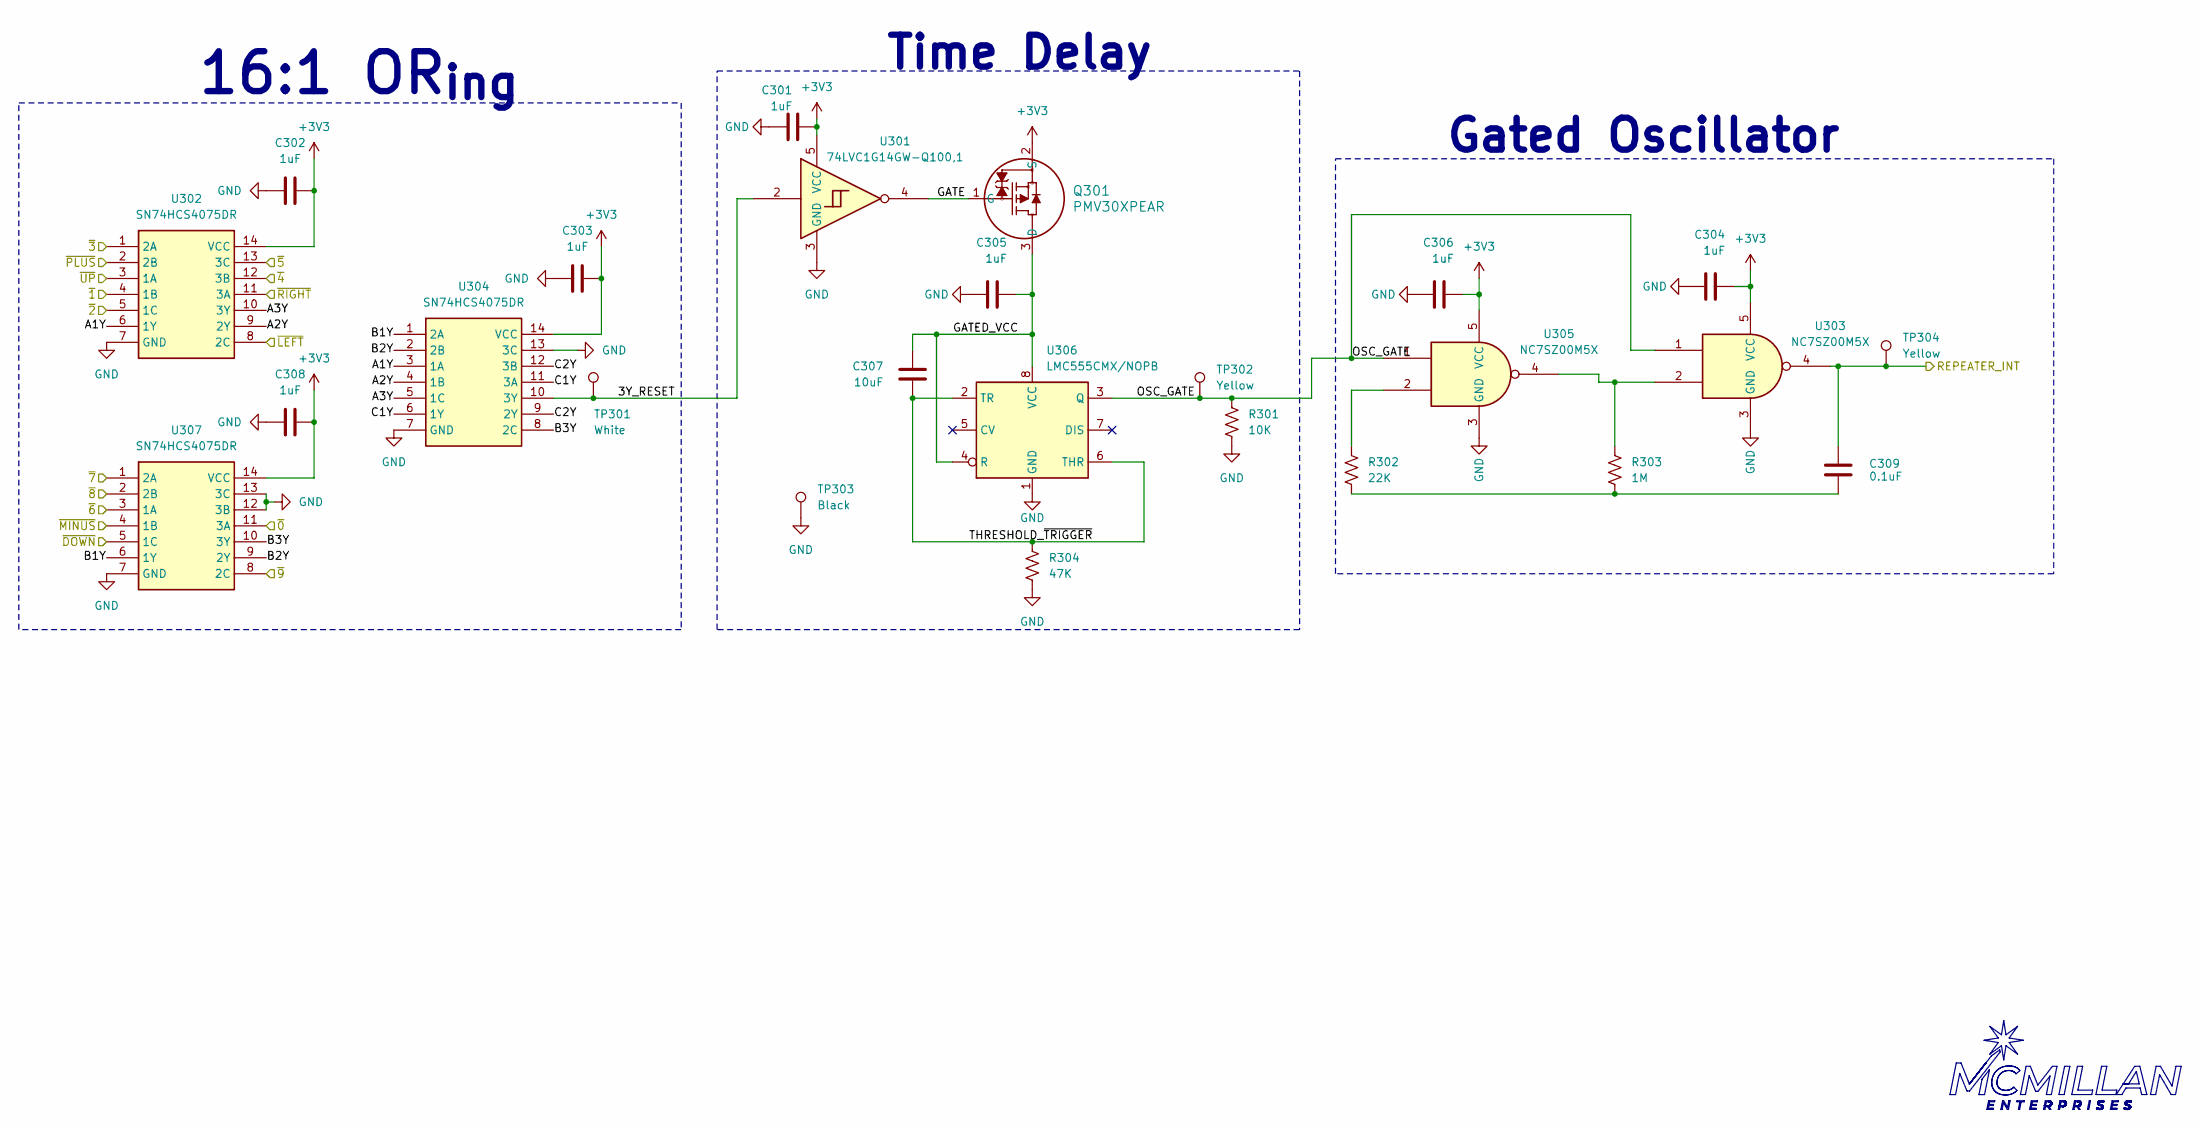
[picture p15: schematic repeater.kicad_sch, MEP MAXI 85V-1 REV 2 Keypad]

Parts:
C301, C302, C303, C304, C305, C306, C308: 1uF; C_0805_2012Metric
C307: 10uF; C_0805_2012Metric
C309: 0.1uF; C_0805_2012Metric
Q301: PMV30XPEAR; SOT-23-3
R301: 10K; R_0805_2012Metric
R302: 22K; R_0805_2012Metric
R303: 1M; R_0805_2012Metric
R304: 47K; R_0805_2012Metric
TP301: White; TestPoint_Keystone_5000-5004_Miniature
TP302, TP304: Yellow; TestPoint_Keystone_5000-5004_Miniature
TP303: Black; TestPoint_Keystone_5000-5004_Miniature
U301: 74LVC1G14GW-Q100,1; SOT-353_SC-70-5
U302, U304, U307: SN74HCS4075DR; SOIC127P600X175-14N; Mouser Part Number 595-SN74HCS4075DR
U303, U305: NC7SZ00M5X; SOT-23-5
U306: LMC555CMX/NOPB; SOIC-8_3.9x4.9mm_P1.27mm

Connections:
+3V3: C301.1, C302.2, C303.2, C304.1, C306.1, C308.2, Q301.2 (S), U301.5 (VCC), U302.14 (VCC), U303.5 (VCC), U304.14 (VCC), U305.5 (VCC), U307.14 (VCC); also elsewhere on the board
/Debounce Switches/~0: U307.11 (3A); also elsewhere on the board
/Debounce Switches/~1: U302.4 (1B); also elsewhere on the board
/Debounce Switches/~2: U302.5 (1C); also elsewhere on the board
/Debounce Switches/~3: U302.1 (2A); also elsewhere on the board
/Debounce Switches/~4: U302.12 (3B); also elsewhere on the board
/Debounce Switches/~5: U302.13 (3C); also elsewhere on the board
/Debounce Switches/~6: U307.3 (1A); also elsewhere on the board
/Debounce Switches/~7: U307.1 (2A); also elsewhere on the board
/Debounce Switches/~8: U307.2 (2B); also elsewhere on the board
/Debounce Switches/~9: U307.8 (2C); also elsewhere on the board
/Debounce Switches/~DOWN: U307.5 (1C); also elsewhere on the board
/Debounce Switches/~LEFT: U302.8 (2C); also elsewhere on the board
/Debounce Switches/~MINUS: U307.4 (1B); also elsewhere on the board
/Debounce Switches/~PLUS: U302.2 (2B); also elsewhere on the board
/Debounce Switches/~RIGHT: U302.11 (3A); also elsewhere on the board
/Debounce Switches/~UP: U302.3 (1A); also elsewhere on the board
/REPEATER_INT: C309.1, TP304.1, U303.4; also elsewhere on the board
/Repeater/3Y_RESET: TP301.1, U301.2, U304.10 (3Y)
/Repeater/A1Y: U302.6 (1Y), U304.3 (1A)
/Repeater/A2Y: U302.9 (2Y), U304.4 (1B)
/Repeater/A3Y: U302.10 (3Y), U304.5 (1C)
/Repeater/B1Y: U304.1 (2A), U307.6 (1Y)
/Repeater/B2Y: U304.2 (2B), U307.9 (2Y)
/Repeater/B3Y: U304.8 (2C), U307.10 (3Y)
/Repeater/C1Y: U304.6 (1Y), U304.11 (3A)
/Repeater/C2Y: U304.9 (2Y), U304.12 (3B)
/Repeater/GATE: Q301.1 (G), U301.4
/Repeater/GATED_VCC: C305.1, C307.1, Q301.3 (D), U306.4 (R), U306.8 (VCC)
/Repeater/OSC_GATE: R301.1, TP302.1, U303.1, U305.1, U306.3 (Q)
/Repeater/THRESHOLD_~TRIGGER: C307.2, R304.1, U306.2 (TR), U306.6 (THR)
GND: C301.2, C302.1, C303.1, C304.2, C305.2, C306.2, C308.1, R301.2, R304.2, TP303.1, U301.3 (GND), U302.7 (GND), U303.3 (GND), U304.7 (GND), U304.13 (3C), U305.3 (GND), U306.1 (GND), U307.7 (GND), U307.12 (3B), U307.13 (3C); also elsewhere on the board
unnamed: C309.2, R302.2, R303.2
unnamed: R302.1, U305.2
unnamed: R303.1, U303.2, U305.4

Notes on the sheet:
Gated Oscillator
Time Delay
16:1 OR_{ing}

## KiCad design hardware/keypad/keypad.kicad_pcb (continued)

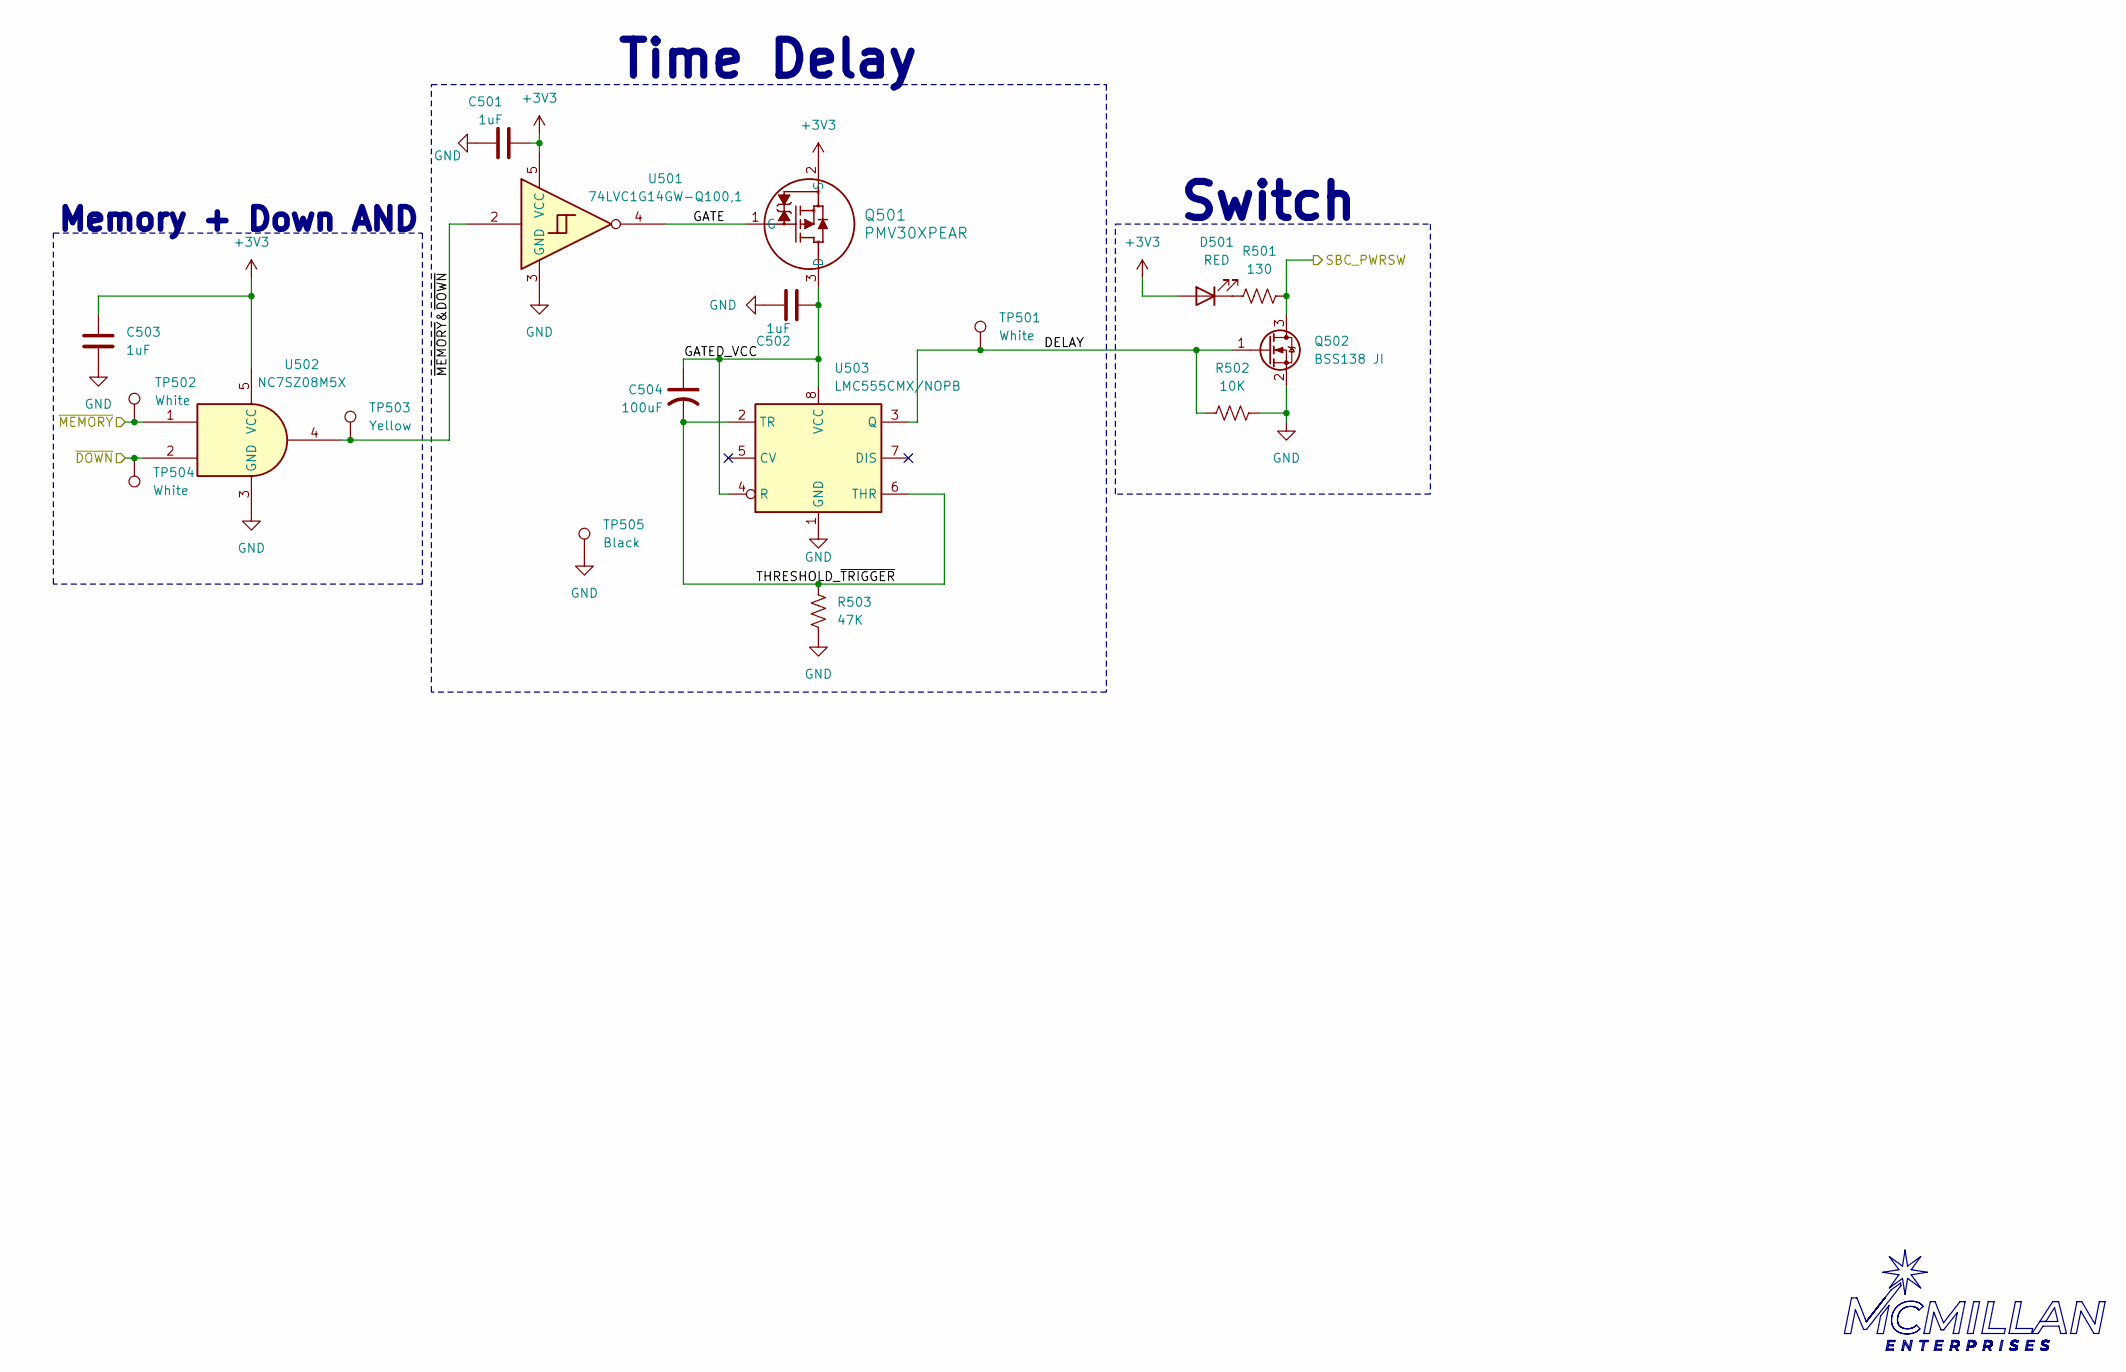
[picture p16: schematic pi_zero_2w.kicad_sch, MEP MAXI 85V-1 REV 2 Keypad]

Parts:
C501, C502, C503: 1uF; C_0805_2012Metric
C504: 100uF; C_Elec_6.3x5.4
D501: RED; LED_1206_3216Metric
Q501: PMV30XPEAR; SOT-23-3
Q502: BSS138 JI; SOT-23
R501: 130; R_0805_2012Metric
R502: 10K; R_0805_2012Metric
R503: 47K; R_0805_2012Metric
TP501, TP502, TP504: White; TestPoint_Keystone_5000-5004_Miniature
TP503: Yellow; TestPoint_Keystone_5000-5004_Miniature
TP505: Black; TestPoint_Keystone_5000-5004_Miniature
U501: 74LVC1G14GW-Q100,1; SOT-353_SC-70-5
U502: NC7SZ08M5X; SC-74A-5_1.55x2.9mm_P0.95mm
U503: LMC555CMX/NOPB; SOIC-8_3.9x4.9mm_P1.27mm

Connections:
+3V3: C501.1, C503.1, D501.2 (A), Q501.2 (S), U501.5 (VCC), U502.5 (VCC); also elsewhere on the board
/Debounce Switches/~DOWN: TP504.1, U502.2; also elsewhere on the board
/Debounce Switches/~MEMORY: TP502.1, U502.1; also elsewhere on the board
/PWRSW: Q502.3 (D), R501.1; also elsewhere on the board
/Pi Zero 2W Power Reset/DELAY: Q502.1 (G), R502.2, TP501.1, U503.3 (Q)
/Pi Zero 2W Power Reset/GATE: Q501.1 (G), U501.4
/Pi Zero 2W Power Reset/GATED_VCC: C502.1, C504.1, Q501.3 (D), U503.4 (R), U503.8 (VCC)
/Pi Zero 2W Power Reset/THRESHOLD_~TRIGGER: C504.2, R503.1, U503.2 (TR), U503.6 (THR)
/Pi Zero 2W Power Reset/~MEMORY&~DOWN: TP503.1, U501.2, U502.4
GND: C501.2, C502.2, C503.2, Q502.2 (S), R502.1, R503.2, TP505.1, U501.3 (GND), U502.3 (GND), U503.1 (GND); also elsewhere on the board
unnamed: D501.1 (K), R501.2

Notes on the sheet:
Switch
Time Delay
Memory + Down AND

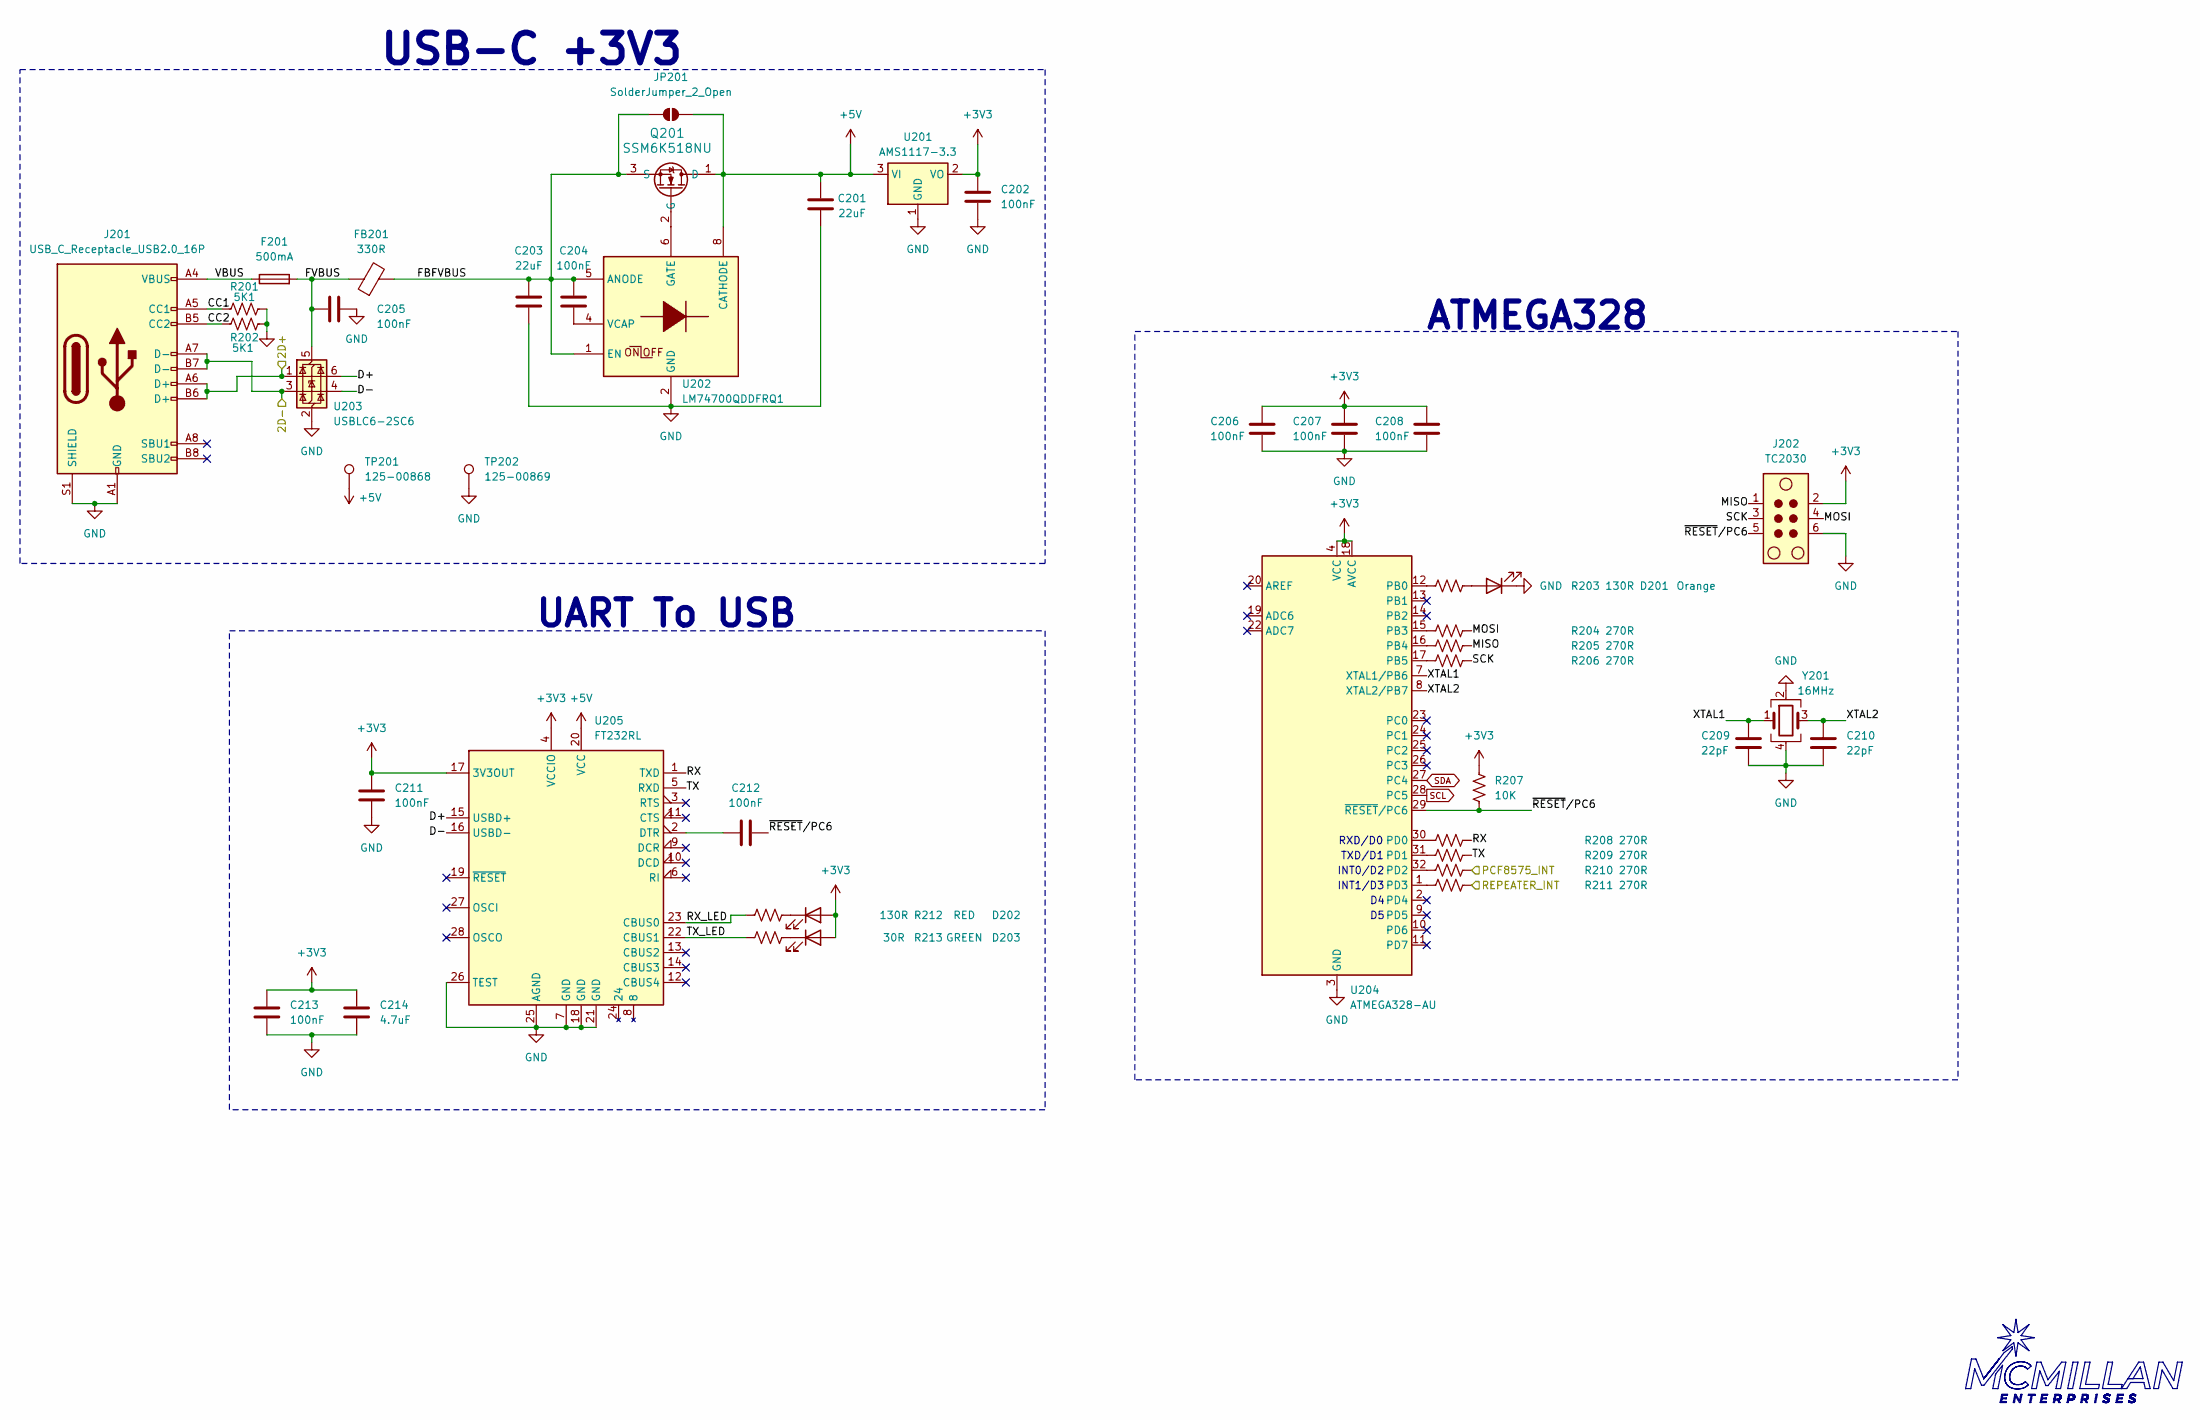
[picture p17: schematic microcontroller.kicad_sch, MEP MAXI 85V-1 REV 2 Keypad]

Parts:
C201, C203: 22uF; C_1206_3216Metric
C202, C205, C206, C207, C208, C211, C212, C213: 100nF; C_0805_2012Metric
C204: 100nF; C_1206_3216Metric
C209, C210: 22pF; C_0805_2012Metric
C214: 4.7uF; C_0805_2012Metric
D201: Orange; LED_0805_2012Metric
D202: RED; LED_0805_2012Metric
D203: GREEN; LED_0805_2012Metric
F201: 500mA; Fuse_0805_2012Metric
FB201: 330R; L_0805_2012Metric
J201: USB_C_Receptacle_USB2.0_16P; USB_C_Receptacle_G-Switch_GT-USB-7010ASV
J202: TC2030; Tag-Connect_TC2030-IDC-NL_2x03_P1.27mm_Vertical
JP201: SolderJumper_2_Open; SolderJumper-2_P1.3mm_Open_TrianglePad1.0x1.5mm
Q201: SSM6K518NU; SOT-1220UDFN6B_TOS
R201, R202: 5K1; R_0805_2012Metric
R203, R212: 130R; R_0805_2012Metric
R204, R205, R206, R208, R209, R210, R211: 270R; R_0805_2012Metric
R207: 10K; R_0805_2012Metric
R213: 30R; R_0805_2012Metric
TP201: 125-00868; TestPoint_Keystone_5000-5004_Miniature
TP202: 125-00869; TestPoint_Keystone_5000-5004_Miniature
U201: AMS1117-3.3; SOT-223-3_TabPin2
U202: LM74700QDDFRQ1; SOT65P280X110-8N; Mouser Part Number 595-LM74700QDDFRQ1
U203: USBLC6-2SC6; SOT-23-6
U204: ATMEGA328-AU; TQFP-32_7x7mm_P0.8mm
U205: FT232RL; SSOP-28_5.3x10.2mm_P0.65mm
Y201: 16MHz; Crystal_SMD_3225-4Pin_3.2x2.5mm

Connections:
+3V3: C202.1, C206.1, C207.1, C208.1, C211.1, C213.1, C214.1, D202.2 (A), D203.2 (A), J202.2, R207.1, U201.2 (VO), U204.4 (VCC), U204.6 (VCC), U204.18 (AVCC), U205.4 (VCCIO), U205.17 (3V3OUT); also elsewhere on the board
/Microcontroller/CC1: J201.A5 (CC1), R201.2
/Microcontroller/CC2: J201.B5 (CC2), R202.2
/Microcontroller/D+: U203.6 (I/O1), U205.15 (USBD+)
/Microcontroller/D-: U203.4 (I/O2), U205.16 (USBD-)
/Microcontroller/FBFVBUS: C203.1, C204.1, FB201.2, JP201.1 (A), Q201.3 (S), U202.1 (EN), U202.5 (ANODE)
/Microcontroller/FVBUS: C205.2, F201.2, FB201.1, U203.5 (VBUS)
/Microcontroller/MISO: J202.1, R205.2
/Microcontroller/MOSI: J202.4, R204.2
/Microcontroller/RX: R208.2, U205.1 (TXD)
/Microcontroller/RX_LED: R212.2, U205.23 (CBUS0)
/Microcontroller/SCK: J202.3, R206.2
/Microcontroller/TX: R209.2, U205.5 (RXD)
/Microcontroller/TX_LED: R213.2, U205.22 (CBUS1)
/Microcontroller/VBUS: F201.1, J201.A4 (VBUS), J201.A9 (VBUS), J201.B4 (VBUS), J201.B9 (VBUS)
/Microcontroller/XTAL1: C209.1, U204.7 (XTAL1/PB6), Y201.1
/Microcontroller/XTAL2: C210.1, U204.8 (XTAL2/PB7), Y201.3
/Microcontroller/~RESET/PC6: C212.2, J202.5, R207.2, U204.29 (~RESET/PC6)
/PCF8575_INT: R210.2; also elsewhere on the board
/REPEATER_INT: R211.2; also elsewhere on the board
/USB3-D+: J201.A6 (D+), J201.B6 (D+), U203.1 (I/O1); also elsewhere on the board
/USB3-D-: J201.A7 (D-), J201.B7 (D-), U203.3 (I/O2); also elsewhere on the board
GND: C201.2, C202.2, C203.2, C205.1, C206.2, C207.2, C208.2, C209.2, C210.2, C211.2, C213.2, C214.2, D201.1 (K), J201.A1 (GND), J201.A12 (GND), J201.B1 (GND), J201.B12 (GND), J201.S1 (SHIELD), J202.6, R201.1, R202.1, TP202.1, U201.1 (GND), U202.2 (GND), U203.2 (GND), U204.3 (GND), U204.5 (GND), U204.21 (GND), U205.7 (GND), U205.18 (GND), U205.21 (GND), U205.25 (AGND), U205.26 (TEST), Y201.2, Y201.4; also elsewhere on the board
unnamed: D201.2 (A), R203.2
unnamed: D202.1 (K), R212.1
unnamed: D203.1 (K), R213.1
unnamed: C204.2, U202.4 (VCAP)
unnamed: R203.1, U204.12 (PB0)
unnamed: R204.1, U204.15 (PB3)
unnamed: R205.1, U204.16 (PB4)
unnamed: R206.1, U204.17 (PB5)
unnamed: R208.1, U204.30 (PD0)
unnamed: R209.1, U204.31 (PD1)
unnamed: R210.1, U204.32 (PD2)
unnamed: R211.1, U204.1 (PD3)
unnamed: C212.1, U205.2 (DTR)
SCL: U204.28 (PC5); also elsewhere on the board
SDA: U204.27 (PC4); also elsewhere on the board

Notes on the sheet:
RXD/D0
INT1/D3
ATMEGA328
INT0/D2
USB-C +3V3
UART To USB
TXD/D1

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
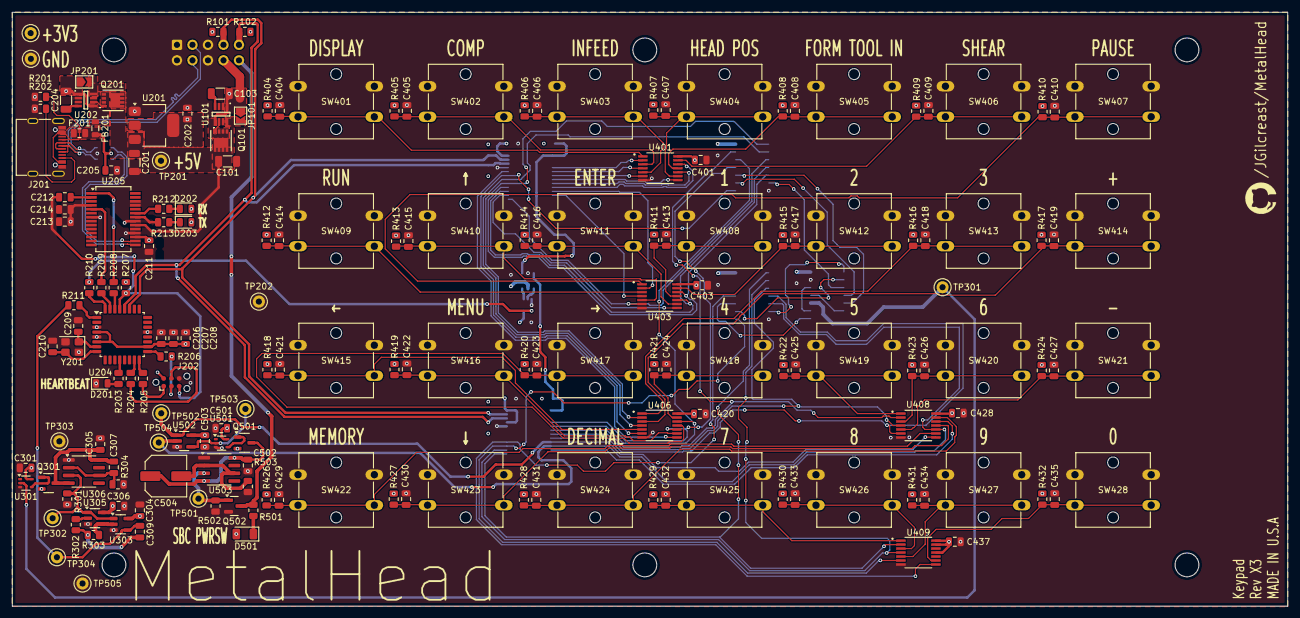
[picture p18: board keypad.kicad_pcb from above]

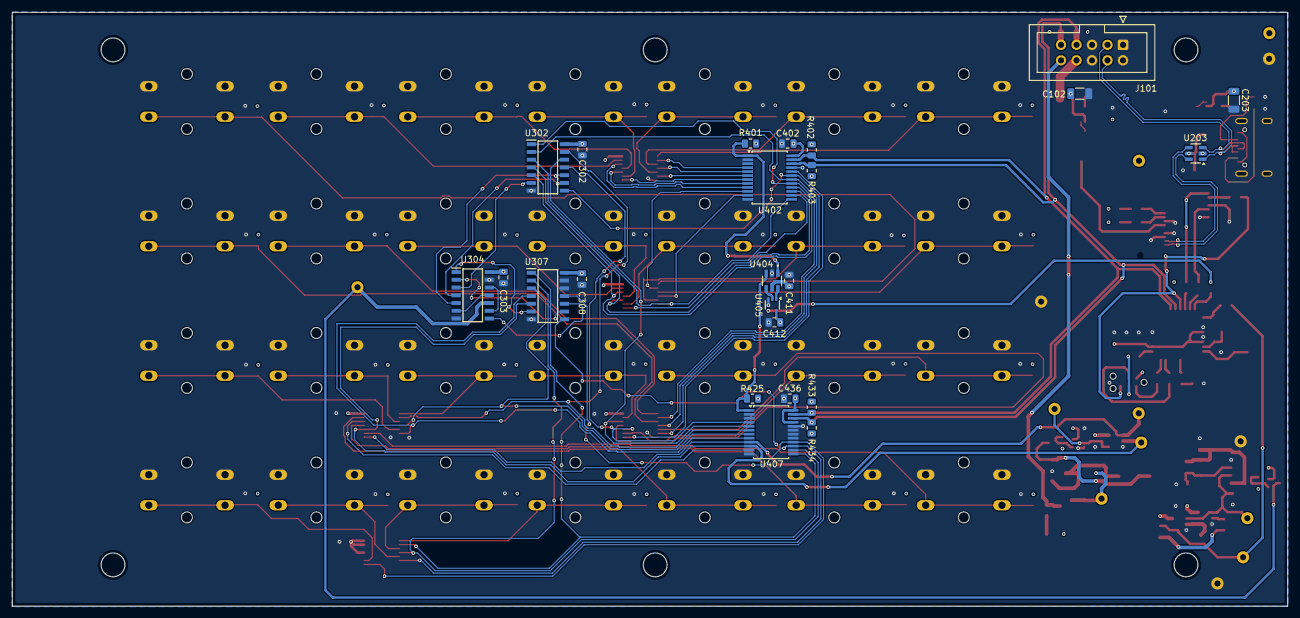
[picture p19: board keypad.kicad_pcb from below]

Board: 4 copper layers, 209.0 x 97.3 mm, 206 parts (24 on the bottom side), 126 nets.

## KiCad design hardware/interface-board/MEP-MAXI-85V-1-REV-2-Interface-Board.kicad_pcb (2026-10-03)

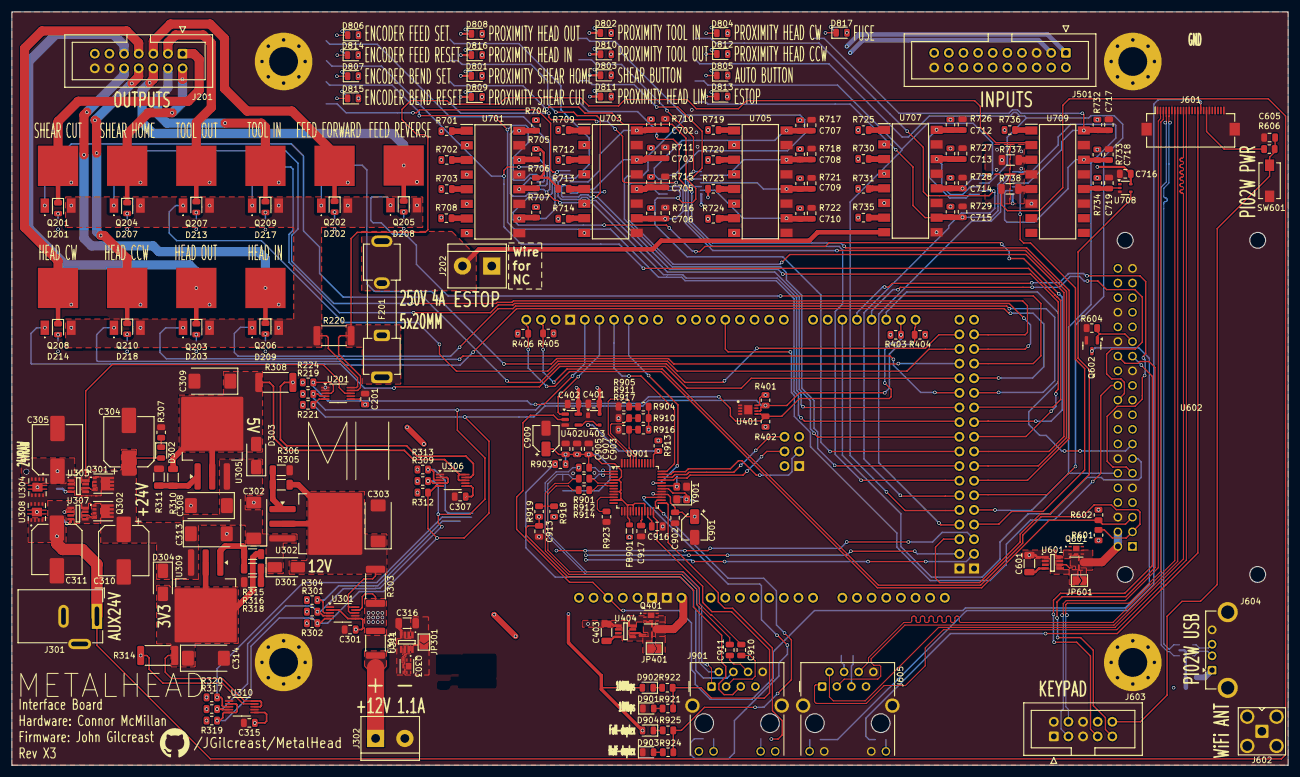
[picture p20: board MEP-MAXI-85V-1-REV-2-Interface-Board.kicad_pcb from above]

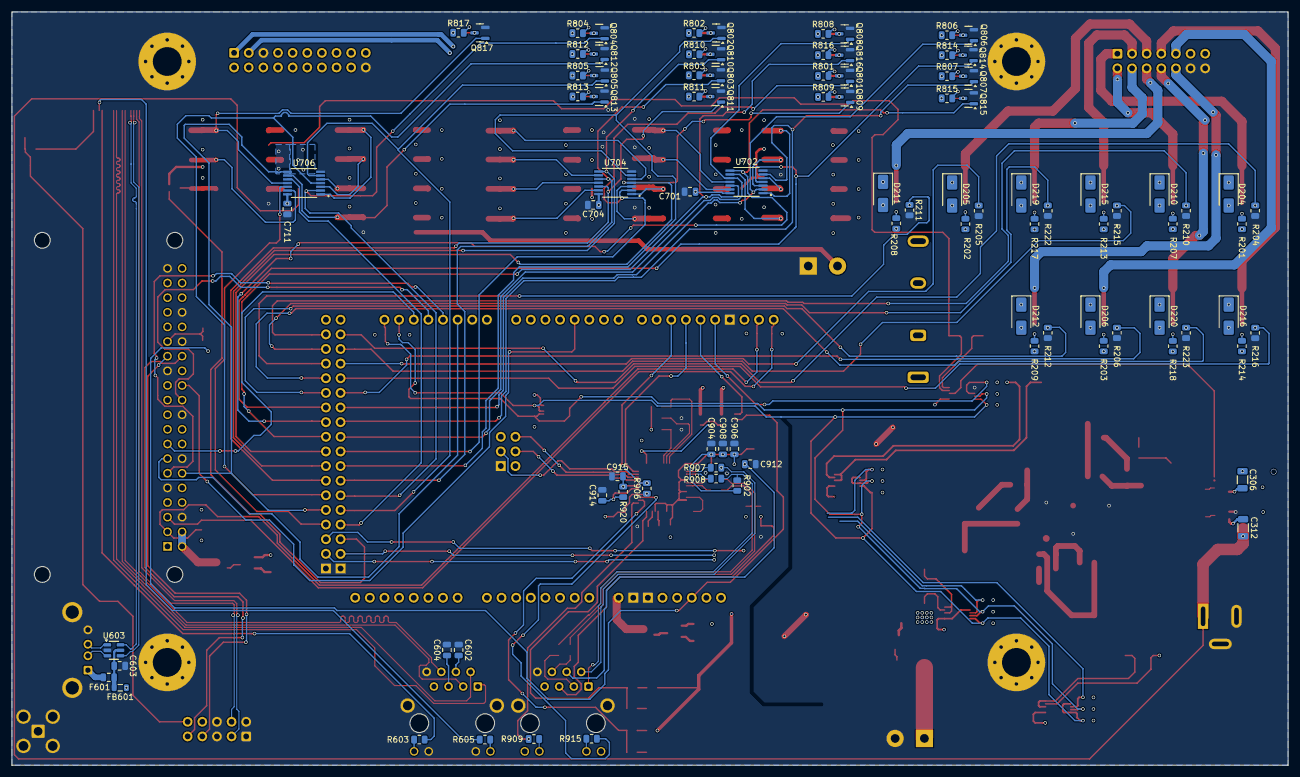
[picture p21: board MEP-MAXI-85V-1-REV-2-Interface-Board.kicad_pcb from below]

Board: 4 copper layers, 221.5 x 130.8 mm, 330 parts (93 on the bottom side), 244 nets.

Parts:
A401: Arduino_Due_Shield
C201, C301, C307, C315, C902, C903, C904, C905, C906, C907, C908: 0.1uF; C_0805_2012Metric
C302, C303, C308, C309, C313, C314: 10uF 50V; CP_EIA-7343-31_Kemet-D
C304, C305, C310, C311: 330uF 25V; CP_Elec_8x10.5
C306, C312, C316, C403, C601: 100nF; C_1206_3216Metric
C401, C402, C701, C702, C703, C704, C705, C706, C707, C708, C709, C710, C711, C712, C713, C714, C715, C716, C717, C718, C719: 1uF; C_0805_2012Metric
C602, C603, C604, C605: 100nF; C_0805_2012Metric
C901, C909: 10uF; CP_Elec_4x5.4
C910, C911: 6.8nF; C_0805_2012Metric
C912: 22nF; C_0805_2012Metric
C913, C916: 10nF; C_0805_2012Metric
C914, C915: 18pF; C_0805_2012Metric
C917: 4.7uF; C_0805_2012Metric
D201, D202, D203, D207, D208, D209, D213, D214, D217, D218, D901, D902, D903, D904: RED; LED_0805_2012Metric
D204, D205, D206, D210, D211, D212, D215, D216, D219, D220: SMAJ24A; D_SMA
D301, D303, D304: 1N4002 M2; D_SMA
D302, D801, D802, D803, D804, D805, D806, D807, D808, D809, D810, D811, D812, D813, D814, D815, D816, D817: BLUE; LED_0805_2012Metric
F201: 3512P; Fuseholder_Clip-5x20mm_Keystone_3512P_Inline_P23.62x7.27mm_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
F301: 16V/1.1A; Fuse_1812_4532Metric
F601: 500mA; Fuse_0805_2012Metric
FB601: 330R; L_0805_2012Metric
FB901: 120R; L_0805_2012Metric
H101, H102, H103, H104: MountingHole_Pad; MountingHole_5mm_Pad_Via
J201: Conn_02x07_Odd_Even; IDC-Header_2x07_P2.54mm_Vertical
J202, J302: Screw_Terminal_01x02; TerminalBlock_bornier-2_P5.08mm
J301: Barrel_Jack_MountingPin; BarrelJack_Wuerth_6941xx301002
J501: Conn_02x10_Odd_Even; IDC-Header_2x10_P2.54mm_Vertical
J601: Conn_01x24_MountingPin; Hirose_FH12-24S-0.5SH_1x24-1MP_P0.50mm_Horizontal
J602: Conn_Coaxial; SMA_Amphenol_901-143_Horizontal
J603: Conn_02x05_Odd_Even; IDC-Header_2x05_P2.54mm_Vertical
J604: USB_A; USB_A_Connfly_DS1095
J605, J901: RJ45_Hanrun_HR911105A_Horizontal
JP301, JP401, JP601: SolderJumper_2_Open; SolderJumper-2_P1.3mm_Open_TrianglePad1.0x1.5mm
Q201, Q202, Q203, Q204, Q205, Q206, Q207, Q208, Q209, Q210: IRFR7540TRPBF
Q301, Q302: DMT6007LFG; DMP4013LFG7
Q303, Q401, Q601: SSM6K518NU; SOT-1220UDFN6B_TOS
Q602, Q801, Q802, Q803, Q804, Q805, Q806, Q807, Q808, Q809, Q810, Q811, Q812, Q813, Q814, Q815, Q816, Q817: BSS138 JI; SOT-23
R201, R202, R203, R207, R208, R209, R213, R214, R217, R218, R801, R802, R803, R804, R805, R806, R807, R808, R809, R810, R811, R812, R813, R814, R815, R816, R817: 200R; R_0805_2012Metric
R204, R205, R206, R210, R211, R212, R215, R216, R219, R221, R222, R223, R224, R301, R302, R304, R309, R312, R313, R317, R319, R320, R401, R402, R403, R404, R604, R906, R913: 10K; R_0805_2012Metric
R220, R303, R308, R314: 2mR; R_2512_6332Metric
R305, R310, R315: 300R; R_1206_3216Metric
R306: 2K580; R_1206_3216Metric
R307: 2K2; R_0805_2012Metric
R311: 900R; R_1206_3216Metric
R316: 470R; R_1206_3216Metric
R318: 22R; R_1206_3216Metric
R405, R406, R601, R602: 4K7; R_0805_2012Metric
R603, R605, R606: 510R; R_0805_2012Metric
R701, R702, R703, R708, R709, R712, R713, R714, R719, R720, R723, R724, R725, R730, R731, R735, R736: 105R; R_0805_2012Metric
R704, R705, R706, R707, R710, R711, R715, R716, R717, R718, R721, R722, R726, R727, R728, R729, R732, R733, R734: 100K; R_0805_2012Metric
R737, R738: 1K2; R_1206_3216Metric
R901, R902: 49R9; R_0805_2012Metric
R903: 10R; R_0805_2012Metric
R904, R905, R909, R910, R911, R915, R916, R917: 330R; R_0805_2012Metric
R907, R908, R912, R914: 0R; R_0805_2012Metric
R918, R919: 82R; R_0805_2012Metric
R920: 1M; R_0805_2012Metric
R921, R922, R924, R925: 130R; R_0805_2012Metric
R923: 12.4K 1%; R_0805_2012Metric
SW601: SW_SPST_Omron_B3FS-100xP; SW_SPST_EVQPE1
U201, U301, U306, U310: INA226; VSSOP-10_3x3mm_P0.5mm
U302, U305, U309: LM1084-ADJ; TO-263-3_TabPin2
U303, U307, U311, U404, U601: LM74700QDDFRQ1; SOT65P280X110-8N
U304, U308: TVS2701DRBR; IC_TVS2701DRBR
U401: AT24C256C-MAHL-E; SON50P300X200X60-9L
U402: NC7SZ08M5X; SOT-23-5
U403: APX811-31UG-7; SOT-143
U602: RASPBERRY_PI_ZERO_2_W; MODULE_RASPBERRY_PI_ZERO_2_W
U603: USBLC6-2SC6; SOT-23-6
U701, U703, U705, U707, U709: LTV-846S; LTV846S
U702, U704, U706: SN74HC14PWR; SOP65P640X120-14N
U708: 74LVC1G14GW-Q100,1; SOT-353_SC-70-5
U901: W5500; LQFP-48_7x7mm_P0.5mm
Y901: 25MHz; Crystal_SMD_3225-4Pin_3.2x2.5mm

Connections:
24VRAW: C305.1, C306.1, J201.11, J501.6, Q301.1 (S), R737.1, U303.1 (EN), U303.5 (ANODE), U304.1 (IN), U304.2 (IN), U304.3 (IN), U304.4 (IN)
+3V3: C201.2, C301.2, C307.2, C315.2, C401.2, C402.2, C701.2, C704.2, C711.2, C716.1, C901.1, C902.1, D902.2 (A), D904.2 (A), FB901.1, J901.9, J901.12, R219.2, R221.1, R224.1, R301.2, R302.1, R304.1, R309.2, R312.1, R313.1, R314.2, R317.2, R319.1, R320.1, R401.1, R402.2, R403.2, R404.1, R405.2, R406.1, R601.2, R602.1, R701.1, R702.1, R703.1, R704.1, R705.1, R706.1, R707.1, R708.1, R709.1, R710.1, R711.1, R712.1, R713.1, R714.1, R715.1, R716.1, R717.1, R718.1, R719.1, R720.1, R721.1, R722.1, R723.1, R724.1, R725.1, R726.1, R727.1, R728.1, R729.1, R730.1, R731.1, R732.1, R733.1, R734.1, R735.1, R736.1, R904.2, R906.2, R910.2, R913.2, R916.2, U201.6 (VS), U301.2 (A0), U301.6 (VS), U306.6 (VS), U310.6 (VS), U310.9 (Vin-), U401.8 (VCC), U402.5 (VCC), U403.4 (VCC), U702.14 (VCC), U704.14 (VCC), U706.14 (VCC), U708.5 (VCC), U901.28 (VDD)
+3V3A: C903.1, C904.1, C905.1, C906.1, C907.1, C908.1, C909.1, FB901.2, R901.2, R902.2, R903.2, U901.4 (AVDD), U901.8 (AVDD), U901.11 (AVDD), U901.15 (AVDD), U901.17 (AVDD), U901.21 (AVDD)
+5V: C601.1, JP601.1 (A), Q601.1 (D), R201.1, R202.1, R203.1, R207.1, R208.1, R209.1, R213.1, R214.1, R217.1, R218.1, R308.2, R801.2, R802.2, R803.2, R804.2, R805.2, R806.2, R807.2, R808.2, R809.2, R810.2, R811.2, R812.2, R813.2, R814.2, R815.2, R816.2, R817.2, U306.9 (Vin-), U601.1 (EN), U601.5 (ANODE)
+12V: C316.1, C403.1, JP301.1 (A), JP401.1 (A), Q303.3 (S), Q401.1 (D), R303.2, U301.9 (Vin-), U311.1 (EN), U311.5 (ANODE), U404.1 (EN), U404.5 (ANODE)
+24V: C302.1, C304.1, C308.1, C310.1, C313.1, D301.1 (K), D302.2 (A), D303.1 (K), D304.1 (K), Q301.3 (D), Q302.3 (D), U201.8 (Vbus), U302.3 (VI), U303.8 (CATHODE), U305.3 (VI), U307.8 (CATHODE), U309.3 (VI)
/Arduino Due/D4_CS1/PIN4: A401.D4 (D4_CS1), U602.24 (GPIO8/SPI_~CE0)
/Arduino Due/D10/PIN10: A401.D10 (D10_CS0), R906.1, U901.32 (~SCS)
/Arduino Due/D11/PIN11: A401.D11, U901.36 (~INT)
/Arduino Due/D12/PIN12: A401.D12, U402.1
/Arduino Due/D13/PIN13: A401.D13, R224.2, U201.3 (~Alert)
/Arduino Due/D22/PIN22: A401.D22, Q201.1 (G), R204.2
/Arduino Due/D23/PIN23: A401.D23, Q204.1 (G), R210.2
/Arduino Due/D24/PIN24: A401.D24, Q207.1 (G), R215.2
/Arduino Due/D25/PIN25: A401.D25, Q209.1 (G), R222.2
/Arduino Due/D26/PIN26: A401.D26, Q202.1 (G), R205.2
/Arduino Due/D27/PIN27: A401.D27, Q205.1 (G), R211.2
/Arduino Due/D28/PIN28: A401.D28, Q208.1 (G), R216.2
/Arduino Due/D29/PIN29: A401.D29, Q210.1 (G), R223.2
/Arduino Due/D30/PIN30: A401.D30, Q203.1 (G), R206.2
/Arduino Due/D31/PIN31: A401.D31, Q206.1 (G), R212.2
/Arduino Due/D32/PIN32: A401.D32, Q806.1 (G), U702.2 (1Y)
/Arduino Due/D33/PIN33: A401.D33, Q814.1 (G), U702.4 (2Y)
/Arduino Due/D34/PIN34: A401.D34, Q807.1 (G), U702.6 (3Y)
/Arduino Due/D35/PIN35: A401.D35, Q815.1 (G), U702.8 (4Y)
/Arduino Due/D36/PIN36: A401.D36, Q808.1 (G), U702.10 (5Y)
/Arduino Due/D37/PIN37: A401.D37, Q816.1 (G), U702.12 (6Y)
/Arduino Due/D38/PIN38: A401.D38, Q801.1 (G), U704.2 (1Y)
/Arduino Due/D39/PIN39: A401.D39, Q809.1 (G), U704.4 (2Y)
/Arduino Due/D40/PIN40: A401.D40, Q802.1 (G), U704.6 (3Y)
/Arduino Due/D41/PIN41: A401.D41, Q810.1 (G), U704.8 (4Y)
/Arduino Due/D42/PIN42: A401.D42, Q803.1 (G), U704.10 (5Y)
/Arduino Due/D43/PIN43: A401.D43, Q811.1 (G), U704.12 (6Y)
/Arduino Due/D44/PIN44: A401.D44, Q804.1 (G), U706.2 (1Y)
/Arduino Due/D45/PIN45: A401.D45, Q812.1 (G), U706.4 (2Y)
/Arduino Due/D46/PIN46: A401.D46, Q805.1 (G), U706.6 (3Y)
/Arduino Due/D47/PIN47: A401.D47, U602.12 (GPIO18/GPIO_GEN1), U706.8 (4Y)
/Arduino Due/D48/PIN48: A401.D48, U706.10 (5Y)
/Arduino Due/D49/PIN49: A401.D49, U706.12 (6Y)
/Arduino Due/D50/PIN50: A401.D50, U708.4
/Arduino Due/D51/PIN51: A401.D51, R304.2, U301.3 (~Alert)
/Arduino Due/D52/PIN52: A401.D52 (D52_CS2), R313.2, U306.3 (~Alert)
/Arduino Due/D53/PIN53: A401.D53, R320.2, U310.3 (~Alert)
/Arduino Due/HMI_I2C_SCL1: A401.SCL1, R406.2, R602.2, U602.5 (GPIO3/SCL)
/Arduino Due/HMI_I2C_SDA1: A401.SDA1, R405.1, R601.1, U602.3 (GPIO2/SDA1)
/Arduino Due/HMI_UART_RX1: A401.D19 (D19/RX1), U602.15 (GPIO22/GPIO_GEN3)
/Arduino Due/HMI_UART_RX2: A401.D17 (D17/RX2), U602.11 (GPIO17/GPIO_GEN0)
/Arduino Due/HMI_UART_TX1: A401.D18 (D18/TX1), U602.22 (GPIO25/GPIO_GEN6)
/Arduino Due/HMI_UART_TX2: A401.D16 (D16/TX2), U602.13 (GPIO27/GPIO_GEN2)
/Arduino Due/SPI_MISO: A401.MISO (SPI_MISO), U602.21 (GPIO9/SPI_MISO), U901.34 (MISO)
/Arduino Due/SPI_MOSI: A401.MOSI (SPI_MOSI), U602.19 (GPIO10/SPI_MOSI), U901.35 (MOSI)
/Arduino Due/SPI_SCK: A401.SCK (SPI_SCK), U602.23 (GPIO11/SPI_SCLK), U901.33 (SCLK)
/Arduino Due/VIN: A401.VIN, JP401.2 (B), Q401.3 (S), U404.8 (CATHODE)
/Arduino Due/~ATSAM3X8E_RESET: A401.RST1 (RESET), Q602.3 (D), U402.2
/Arduino Due/~W5500_RST: R913.1, U403.2 (~RESET), U901.37 (~RST)
/External Power/3V3OUT: C314.1, D304.2 (A), R314.1, R315.1, U309.2 (VO), U310.8 (Vbus), U310.10 (Vin+)
/External Power/5VOUT: C309.1, D303.2 (A), R308.1, R310.1, U305.2 (VO), U306.8 (Vbus), U306.10 (Vin+)
/External Power/12V: F301.1, JP301.2 (B), Q303.1 (D), U311.8 (CATHODE)
/External Power/12VOUT: C303.1, D301.2 (A), R303.1, R305.1, U301.8 (Vbus), U301.10 (Vin+), U302.2 (VO)
/External Power/+12V-HMI-FUSED: F301.2, J302.1
/Input Connections/AUTO_BUTTON: J501.17, U707.6 (C3)
/Input Connections/ENCODER_BEND_RESET: J501.4, U701.8 (C4)
/Input Connections/ENCODER_BEND_SET: J501.3, U701.6 (C3)
/Input Connections/ENCODER_FEED_RESET: J501.2, U701.4 (C2)
/Input Connections/ENCODER_FEED_SET: J501.1, U701.2 (C1)
/Input Connections/PROXIMITY_HEAD_CCW: J501.16, U707.4 (C2)
/Input Connections/PROXIMITY_HEAD_CW: J501.15, U707.2 (C1)
/Input Connections/PROXIMITY_HEAD_IN: J501.8, U703.4 (C2)
/Input Connections/PROXIMITY_HEAD_LIM: J501.14, U705.8 (C4)
/Input Connections/PROXIMITY_HEAD_OUT: J501.7, U703.2 (C1)
/Input Connections/PROXIMITY_SHEAR_CUT: J501.10, U703.8 (C4)
/Input Connections/PROXIMITY_SHEAR_HOME: J501.9, U703.6 (C3)
/Input Connections/PROXIMITY_TOOL_IN: J501.11, U705.2 (C1)
/Input Connections/PROXIMITY_TOOL_OUT: J501.12, U705.4 (C2)
/Input Connections/SHEAR_BUTTON: J501.13, U705.6 (C3)
/Output Connections/ESTOP: F201.2, J202.2, U707.8 (C4)
/Output Connections/FUSE: F201.1, R220.2, U201.9 (Vin-), U709.2 (C1)
/Output Connections/FUSED_GND: D204.2 (A2), D205.2 (A2), D206.2 (A2), D210.2 (A2), D211.2 (A2), D212.2 (A2), D215.2 (A2), D216.2 (A2), D219.2 (A2), D220.2 (A2), Q201.3 (S), Q202.3 (S), Q203.3 (S), Q204.3 (S), Q205.3 (S), Q206.3 (S), Q207.3 (S), Q208.3 (S), Q209.3 (S), Q210.3 (S), R220.1, U201.10 (Vin+)
/Output Connections/SOL_FEED_FORWARD: D202.1 (K), D205.1 (A1), J201.5, Q202.2 (D)
/Output Connections/SOL_FEED_REVERSE: D208.1 (K), D211.1 (A1), J201.6, Q205.2 (D)
/Output Connections/SOL_HEAD_CCW: D218.1 (K), D220.1 (A1), J201.8, Q210.2 (D)
/Output Connections/SOL_HEAD_CW: D214.1 (K), D216.1 (A1), J201.7, Q208.2 (D)
/Output Connections/SOL_HEAD_IN: D209.1 (K), D212.1 (A1), J201.10, Q206.2 (D)
/Output Connections/SOL_HEAD_OUT: D203.1 (K), D206.1 (A1), J201.9, Q203.2 (D)
/Output Connections/SOL_SHEER_CUT: D201.1 (K), D204.1 (A1), J201.1, Q201.2 (D)
/Output Connections/SOL_SHEER_HOME: D207.1 (K), D210.1 (A1), J201.2, Q204.2 (D)
/Output Connections/SOL_TOOL_IN: D217.1 (K), D219.1 (A1), J201.4, Q209.2 (D)
/Output Connections/SOL_TOOL_OUT: D213.1 (K), D215.1 (A1), J201.3, Q207.2 (D)
/Pi Zero 2W SBC/5V: FB601.2, J603.8, JP601.2 (B), Q601.3 (S), U601.8 (CATHODE), U602.2 (5V_2), U602.4 (5V_4)
/Pi Zero 2W SBC/D+: J604.3 (D+), U603.1 (I/O1)
/Pi Zero 2W SBC/D-: J604.2 (D-), U603.3 (I/O2)
/Pi Zero 2W SBC/EPHY-RXN: J601.7, J605.6 (RD-)
/Pi Zero 2W SBC/EPHY-RXP: J601.8, J605.3 (RD+)
/Pi Zero 2W SBC/EPHY-TXN: J601.10, J605.2 (TD-)
/Pi Zero 2W SBC/EPHY-TXP: J601.11, J605.1 (TD+)
/Pi Zero 2W SBC/PC15: J601.15, R603.2
/Pi Zero 2W SBC/PC16: J601.16, R605.2
/Pi Zero 2W SBC/PI0/ATSAM3X8E-RESET: Q602.1 (G), R604.1, U602.29 (GPIO5)
/Pi Zero 2W SBC/PWRON: J601.18, R606.1
/Pi Zero 2W SBC/PWRSW: C605.1, J603.10, R606.2, SW601.1
/Pi Zero 2W SBC/TWI2_SCL/UART3_TX: J603.9, U602.28 (ID_SC)
/Pi Zero 2W SBC/TWI2_SDA/UART3_RX: J603.7, U602.27 (ID_SD)
/Pi Zero 2W SBC/USB2-D+: J601.5, U603.6 (I/O1)
/Pi Zero 2W SBC/USB2-D-: J601.4, U603.4 (I/O2)
/Pi Zero 2W SBC/USB3-D+: J601.3, J603.4
/Pi Zero 2W SBC/USB3-D-: J601.2, J603.3
/Signal Processing/24VRAW*: C718.1, R733.2, U706.13 (6A), U709.14 (C2)
/Signal Processing/AUTO_BUTTON*: C714.1, R728.2, U706.5 (3A), U707.12 (C3)
/Signal Processing/AUX24V*: C719.1, R734.2, U708.2, U709.12 (C3)
/Signal Processing/ENCODER_BEND_RESET*: R707.2, U701.10 (C4), U702.9 (4A)
/Signal Processing/ENCODER_BEND_SET*: R706.2, U701.12 (C3), U702.5 (3A)
/Signal Processing/ENCODER_FEED_RESET*: R705.2, U701.14 (C2), U702.3 (2A)
/Signal Processing/ENCODER_FEED_SET*: R704.2, U701.16 (C1), U702.1 (1A)
/Signal Processing/ESTOP*: C715.1, Q813.1 (G), R729.2, U706.9 (4A), U707.10 (C4)
/Signal Processing/FUSE*: C717.1, Q817.1 (G), R732.2, U706.11 (5A), U709.16 (C1)
/Signal Processing/PROXIMITY_HEAD_CCW*: C713.1, R727.2, U706.3 (2A), U707.14 (C2)
/Signal Processing/PROXIMITY_HEAD_CW*: C712.1, R726.2, U706.1 (1A), U707.16 (C1)
/Signal Processing/PROXIMITY_HEAD_IN*: C703.1, R711.2, U702.13 (6A), U703.14 (C2)
/Signal Processing/PROXIMITY_HEAD_LIM*: C710.1, R722.2, U704.13 (6A), U705.10 (C4)
/Signal Processing/PROXIMITY_HEAD_OUT*: C702.1, R710.2, U702.11 (5A), U703.16 (C1)
/Signal Processing/PROXIMITY_SHEAR_CUT*: C706.1, R716.2, U703.10 (C4), U704.3 (2A)
/Signal Processing/PROXIMITY_SHEAR_HOME*: C705.1, R715.2, U703.12 (C3), U704.1 (1A)
/Signal Processing/PROXIMITY_TOOL_IN*: C707.1, R717.2, U704.5 (3A), U705.16 (C1)
/Signal Processing/PROXIMITY_TOOL_OUT*: C708.1, R718.2, U704.9 (4A), U705.14 (C2)
/Signal Processing/SHEAR_BUTTON*: C709.1, R721.2, U704.11 (5A), U705.12 (C3)
/WIZnet W5500 ENET PHY/1V2O: C916.1, U901.22 (1V2O)
/WIZnet W5500 ENET PHY/ACTLED: R915.1, U901.27 (ACTLED)
/WIZnet W5500 ENET PHY/DUPLED: R924.1, R925.2, U901.26 (DUPLED)
/WIZnet W5500 ENET PHY/EXRES1: R923.2, U901.10 (EXRES1)
/WIZnet W5500 ENET PHY/LINKLED: R909.1, U901.25 (LINKLED)
/WIZnet W5500 ENET PHY/PMODE0: R904.1, R905.2, U901.45 (PMODE0)
/WIZnet W5500 ENET PHY/PMODE1: R910.1, R911.2, U901.44 (PMODE1)
/WIZnet W5500 ENET PHY/PMODE2: R916.1, R917.2, U901.43 (PMODE2)
/WIZnet W5500 ENET PHY/RCT: C913.1, J901.5 (RCT), R918.1, R919.1
/WIZnet W5500 ENET PHY/RD+: C910.2, J901.3 (RD+)
/WIZnet W5500 ENET PHY/RD-: C911.2, J901.6 (RD-)
/WIZnet W5500 ENET PHY/RX+: C910.1, R914.2, R918.2
/WIZnet W5500 ENET PHY/RX-: C911.1, R912.2, R919.2
/WIZnet W5500 ENET PHY/RXN: R912.1, U901.5 (RXN)
/WIZnet W5500 ENET PHY/RXP: R914.1, U901.6 (RXP)
/WIZnet W5500 ENET PHY/SPDLED: R921.1, R922.2, U901.24 (SPDLED)
/WIZnet W5500 ENET PHY/TD+: J901.1 (TD+), R902.1, R908.2
/WIZnet W5500 ENET PHY/TD-: J901.2 (TD-), R901.1, R907.2
/WIZnet W5500 ENET PHY/TOCAP: C917.1, U901.20 (TOCAP)
/WIZnet W5500 ENET PHY/TXN: R907.1, U901.1 (TXN)
/WIZnet W5500 ENET PHY/TXP: R908.1, U901.2 (TXP)
/WIZnet W5500 ENET PHY/XI: C914.1, R920.1, U901.30 (XI/CLKIN), Y901.1
/WIZnet W5500 ENET PHY/XO: C915.1, R920.2, U901.31 (XO), Y901.3
AUX24V: C311.1, C312.1, J301.1, Q302.1 (S), R738.1, U307.1 (EN), U307.5 (ANODE), U308.1 (IN), U308.2 (IN), U308.3 (IN), U308.4 (IN)
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

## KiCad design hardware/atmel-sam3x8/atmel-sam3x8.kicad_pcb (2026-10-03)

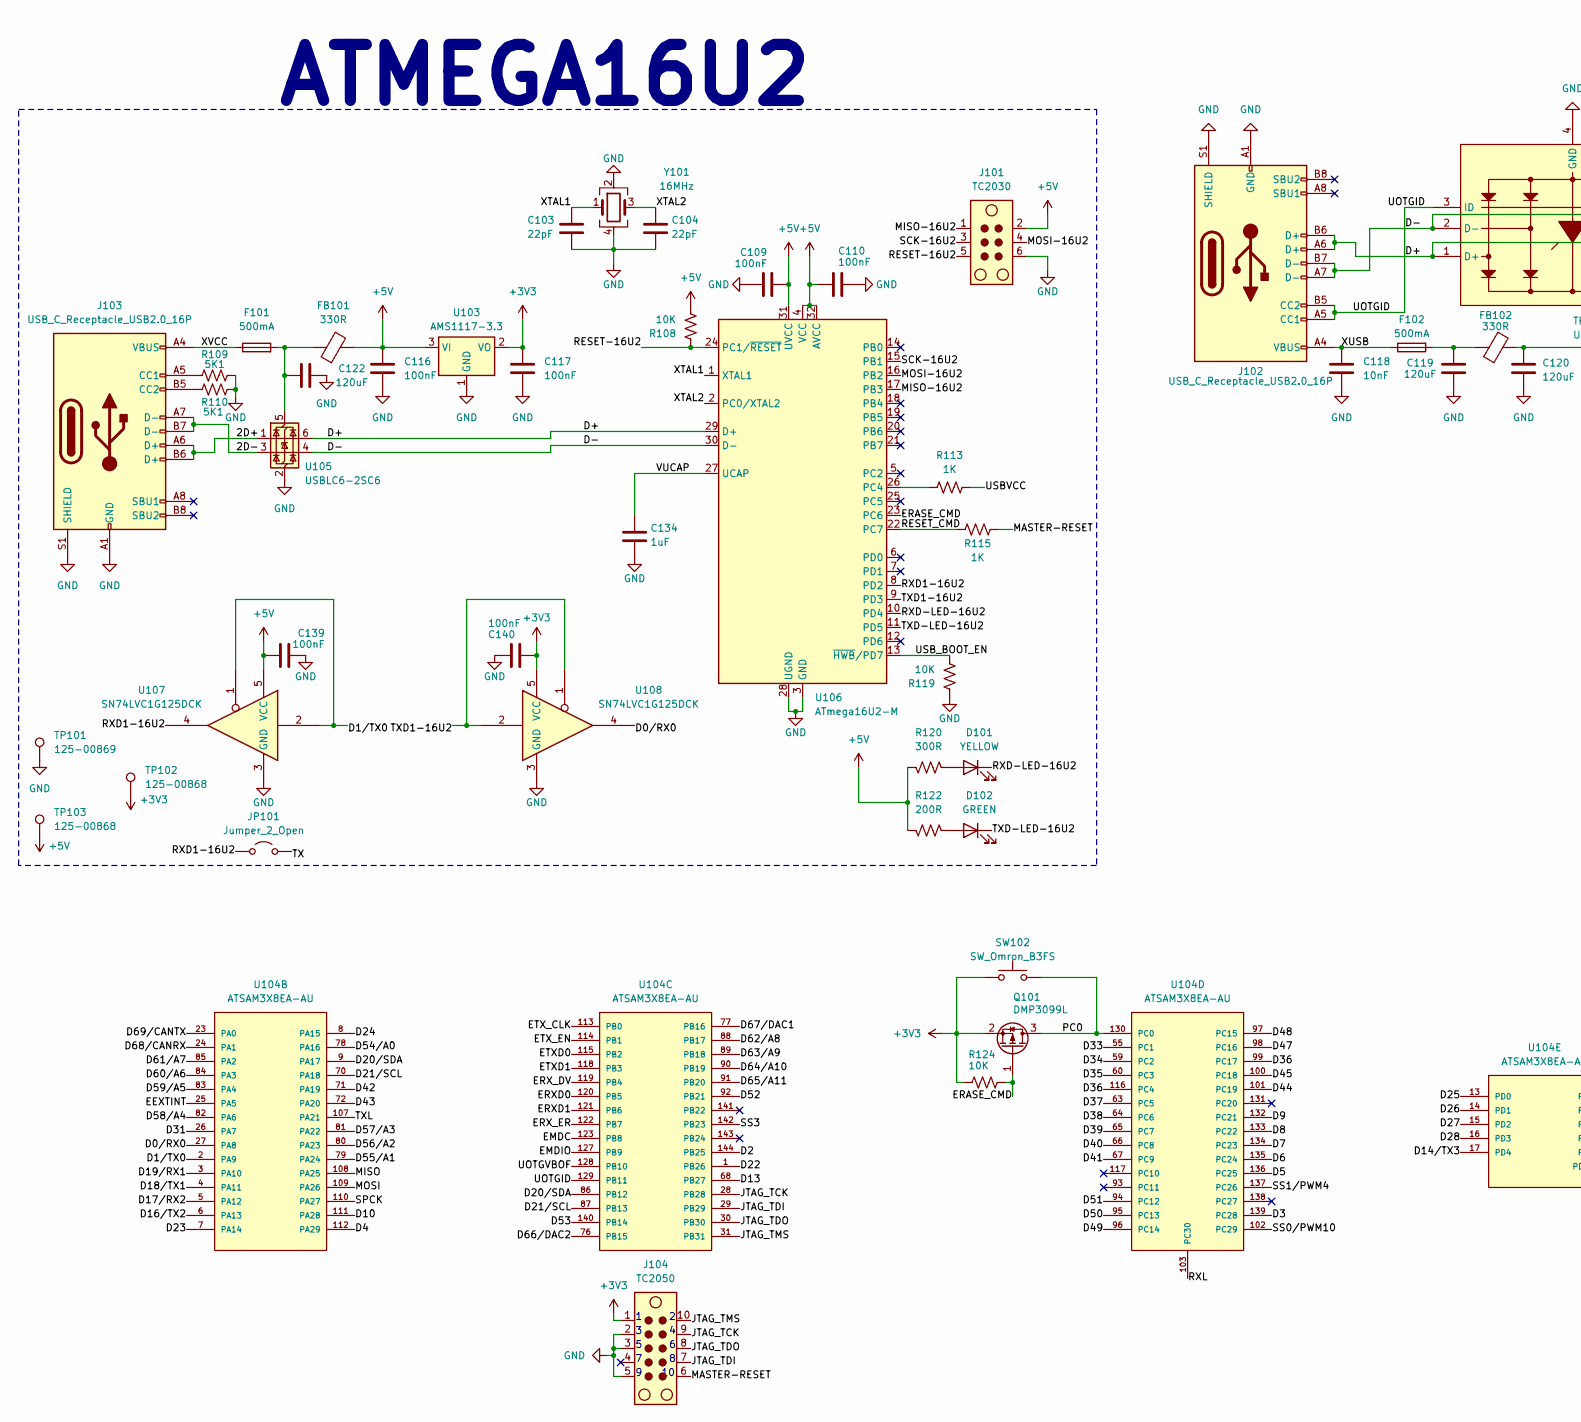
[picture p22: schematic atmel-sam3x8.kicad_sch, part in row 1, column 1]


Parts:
C101, C103, C104: 22pF; C_0805_2012Metric
C102, C108, C133, C144, C145, C146: 4.7uF; C_0805_2012Metric
C105, C106, C107, C109, C110, C111, C112, C115, C116, C117, C123, C124, C126, C128, C130, C131, C132, C135, C136, C137, C138, C139, C140, C141, C142, C143: 100nF; C_0805_2012Metric
C113, C134: 1uF; C_0805_2012Metric
C114, C121, C125, C127: 10pF; C_0805_2012Metric
C118, C129: 10nF; C_0805_2012Metric
C119, C120, C122: 120uF; C_0805_2012Metric
D101: YELLOW; LED_1206_3216Metric
D102: GREEN; LED_1206_3216Metric
F101, F102: 500mA; Fuse_0805_2012Metric
FB101, FB102: 330R; L_0805_2012Metric
J101: TC2030; Tag-Connect_TC2030-IDC-NL_2x03_P1.27mm_Vertical
J102, J103: USB_C_Receptacle_USB2.0_16P; USB_C_Receptacle_G-Switch_GT-USB-7010ASV
J104: TC2050; Tag-Connect_TC2050-IDC-FP_2x05_P1.27mm_Vertical
JP101: Jumper_2_Open; TestPoint_2Pads_Pitch2.54mm_Drill0.8mm
L101, L102, L103: 10uH; L_0805_2012Metric
Q101: DMP3099L; SOT-23-3
R101, R103, R111, R117, R121, R123: 0R; R_0805_2012Metric
R102: 6K8; R_0805_2012Metric
R104, R112, R118: 1R; R_0805_2012Metric
R105, R106: 39R; R_0805_2012Metric
R107, R108, R119, R124: 10K; R_0805_2012Metric
R109, R110: 5K1; R_0805_2012Metric
R113, R115: 1K; R_0805_2012Metric
R114: 0R; R_0805_2012Metric; not fitted
R116: 100K; R_0805_2012Metric
R120: 300R; R_0805_2012Metric
R122: 200R; R_0805_2012Metric
SW101: SW_SPST_Omron_B3FS-100xP; SW_SPST_EVQPE1
SW102: SW_Omron_B3FS; SW_SPST_Omron_B3FS-100xP
TP101: 125-00869; TestPoint_Keystone_5000-5004_Miniature
TP102, TP103: 125-00868; TestPoint_Keystone_5000-5004_Miniature
U101: TPD4S012DRYR; Mouser Part Number 595-TPD4S012DRYR
U102: MIC2005A-2YM5-TR; SOT95P280X145-5N; Mouser Part Number 998-MIC2005A-1YM5TR
U103: AMS1117-3.3; SOT-223-3_TabPin2
U104: ATSAM3X8EA-AU; QFP50P2200X2200X145-144N; PARTREV 11057C
U105: USBLC6-2SC6; SOT-23-6
U106: ATmega16U2-M; QFN-32-1EP_5x5mm_P0.5mm_EP3.6x3.6mm_ThermalVias
U107, U108: SN74LVC1G125DCK; Texas_R-PDSO-G5_DCK-5
Y101: 16MHz; Crystal_SMD_3225-4Pin_3.2x2.5mm
Y102: 12MHz; Crystal_SMD_3225-4Pin_3.2x2.5mm
Y103: 32.768MHz; Crystal_SMD_3225-4Pin_3.2x2.5mm

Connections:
+3V3: C117.1, C129.1, C131.1, C140.1, C142.1, C145.1, C146.1, J104.1, L102.1, L103.1, Q101.2 (S), R107.2, R116.1, R121.2, R123.2, R124.2, SW102.1, TP102.1, U103.2 (VO), U108.5 (VCC)
+5V: C109.1, C110.1, C113.1, C116.1, C139.1, FB101.2, J101.2, R108.2, R120.2, R122.2, TP103.1, U102.1 (VIN), U103.3 (VI), U106.4 (VCC), U106.31 (UVCC), U106.32 (AVCC), U107.5 (VCC)
/2D+: J103.A6 (D+), J103.B6 (D+), U105.1 (I/O1)
/2D-: J103.A7 (D-), J103.B7 (D-), U105.3 (I/O2)
/ADVREF: C143.1, U104.75 (ADVREF)
/D0/RX0: U104.27 (PA8), U108.4
/D1/TX0: U104.2 (PA9), U107.1, U107.2
/D2: U104.144 (PB25)
/D3: U104.139 (PC28)
/D4: U104.112 (PA29)
/D5: U104.136 (PC25)
/D6: U104.135 (PC24)
/D7: U104.134 (PC23)
/D8: U104.133 (PC22)
/D9: U104.132 (PC21)
/D10: U104.111 (PA28)
/D11: U104.20 (PD7)
/D12: U104.21 (PD8)
/D13: U104.68 (PB27)
/D14/TX3: U104.17 (PD4)
/D15/RX3: U104.18 (PD5)
/D16/TX2: U104.6 (PA13)
/D17/RX2: U104.5 (PA12)
/D18/TX1: U104.4 (PA11)
/D19/RX1: U104.3 (PA10)
/D20/SDA: U104.9 (PA17), U104.86 (PB12)
/D21/SCL: U104.70 (PA18), U104.87 (PB13)
/D22: U104.1 (PB26)
/D23: U104.7 (PA14)
/D24: U104.8 (PA15)
/D25: U104.13 (PD0)
/D26: U104.14 (PD1)
/D27: U104.15 (PD2)
/D28: U104.16 (PD3)
/D29: U104.19 (PD6)
/D30: U104.22 (PD9)
/D31: U104.26 (PA7)
/D32: U104.32 (PD10)
/D33: U104.55 (PC1)
/D34: U104.59 (PC2)
/D35: U104.60 (PC3)
/D36: U104.99 (PC17), U104.116 (PC4)
/D37: U104.63 (PC5)
/D38: U104.64 (PC6)
/D39: U104.65 (PC7)
/D40: U104.66 (PC8)
/D41: U104.67 (PC9)
/D42: U104.71 (PA19)
/D43: U104.72 (PA20)
/D44: U104.101 (PC19)
/D45: U104.100 (PC18)
/D47: U104.98 (PC16)
/D48: U104.97 (PC15)
/D49: U104.96 (PC14)
/D50: U104.95 (PC13)
/D51: U104.94 (PC12)
/D52: U104.92 (PB21)
/D53: U104.140 (PB14)
/D54/A0: U104.78 (PA16)
/D55/A1: U104.79 (PA24)
/D56/A2: U104.80 (PA23)
/D57/A3: U104.81 (PA22)
/D58/A4: U104.82 (PA6)
/D59/A5: U104.83 (PA4)
/D60/A6: U104.84 (PA3)
/D61/A7: U104.85 (PA2)
/D62/A8: U104.88 (PB17)
/D63/A9: U104.89 (PB18)
/D64/A10: U104.90 (PB19)
/D65/A11: U104.91 (PB20)
/D66/DAC2: U104.76 (PB15)
/D67/DAC1: U104.77 (PB16)
/D68/CANRX: U104.24 (PA1)
/D69/CANTX: U104.23 (PA0)
/D+: J102.A5 (CC1), J102.A6 (D+), J102.A7 (D-), J102.B5 (CC2), J102.B6 (D+), J102.B7 (D-), R105.2, R106.2, U101.1 (D+), U101.2 (D-), U101.3 (ID), U104.37 (DHSDP), U104.38 (DHSDM), U104.129 (PB11), U105.4 (I/O2), U105.6 (I/O1), U106.29 (D+), U106.30 (D-)
/EEXTINT: U104.25 (PA5)
/EMDC: U104.123 (PB8)
/EMDIO: U104.127 (PB9)
/ERASE_CMD: Q101.1 (G), R124.1, U106.23 (PC6)
/ERXD0: U104.120 (PB5)
/ERXD1: U104.121 (PB6)
/ERX_DV: U104.119 (PB4)
/ERX_ER: U104.122 (PB7)
/ETXD0: U104.115 (PB2)
/ETXD1: U104.118 (PB3)
/ETX_CLK: U104.113 (PB0)
/ETX_EN: U104.114 (PB1)
/FWUP: R116.2, U104.53 (FWUP)
/JTAG_TCK: J104.9, U104.28 (PB28)
/JTAG_TDI: J104.7, U104.29 (PB29)
/JTAG_TDO: J104.8, U104.30 (PB30)
/JTAG_TMS: J104.10, U104.31 (PB31)
/MASTER-RESET: C129.2, J104.6, R115.2, SW101.2, U104.47 (NRSTB)
/MISO: U104.108 (PA25)
/MISO-16U2: J101.1, U106.17 (PB3)
/MOSI: U104.109 (PA26)
/MOSI-16U2: J101.4, U106.16 (PB2)
/PC0: Q101.3 (D), SW102.2, U104.130 (PC0)
/RESET-16U2: J101.5, R108.1, U106.24 (PC1/~RESET)
/RESET_CMD: R115.1, U106.22 (PC7)
/RXD1-16U2: JP101.1 (A), U106.8 (PD2), U107.4
/RXD-LED-16U2: D101.1 (K), U106.10 (PD4)
/RXL: U104.103 (PC30)
/SCK-16U2: J101.3, U106.15 (PB1)
/SPCK: U104.110 (PA27)
/SS0/PWM10: U104.102 (PC29)
/SS1/PWM4: U104.137 (PC26)
/SS3: U104.142 (PB23)
/TST: R114.1, U104.51 (TST)
/TX: JP101.2 (B)
/TXD1-16U2: U106.9 (PD3), U108.1, U108.2
/TXD-LED-16U2: D102.1 (K), U106.11 (PD5)
/TXL: U104.107 (PA21)
/UOTGVBOF: U102.3 (EN), U104.128 (PB10)
/USBVCC: C120.1, FB102.1, R113.2, U101.6 (VBUS), U102.5 (VOUT), U104.39 (VBUS)
/USB_BOOT_EN: R119.2, U106.13 (~HWB/PD7)
/USB_FAULT: R107.1, U102.6 (~FAULT)
/VBG: C101.1, R102.1, U104.40 (VBG)
/VDDANA: C138.1, R117.1, U104.73 (VDDANA)
/VDDBU: C137.1, U104.52 (VDDBU)
/VDDCORE: C107.1, C111.1, C112.1, C115.1, C123.1, R101.2, U104.10 (VDDCORE), U104.45 (VDDCORE), U104.61 (VDDCORE), U104.104 (VDDCORE), U104.124 (VDDCORE)
/VDDIN: R123.1, U104.57 (VDDIN)
/VDDIO: C124.1, C126.1, C128.1, C132.1, R121.1, U104.11 (VDDIO), U104.62 (VDDIO), U104.105 (VDDIO), U104.125 (VDDIO)
/VDDOUT: C102.1, C105.1, L101.2, R101.1, U104.56 (VDDOUT)
/VDDPLL: C135.1, R103.2, U104.34 (VDDPLL)
/VDDUTMI: C136.1, R111.1, U104.41 (VDDUTMI)
/VUCAP: C134.1, U106.27 (UCAP)
/XTAL1: C103.1, U106.1 (XTAL1), Y101.1
/XTAL2: C104.1, U106.2 (PC0/XTAL2), Y101.3
/XUSB: C118.1, F102.1, J102.A4 (VBUS), J102.A9 (VBUS), J102.B4 (VBUS), J102.B9 (VBUS)
/XVCC: F101.1, J103.A4 (VBUS), J103.A9 (VBUS), J103.B4 (VBUS), J103.B9 (VBUS)
GND: C101.2, C102.2, C103.2, C104.2, C105.2, C106.2, C107.2, C108.2, C109.2, C110.2, C111.2, C112.2, C113.2, C114.2, C115.2, C116.2, C117.2, C118.2, C119.1, C120.2, C121.2, C122.1, C123.2, C124.2, C125.2, C126.2, C127.2, C128.2, C130.2, C131.2, C132.2, C133.2, C134.2, C135.2, C136.2, C137.2, C138.2, C139.2, C140.2, C141.2, C142.2, C143.2, C144.2, C145.2, C146.2, J101.6, J102.A1 (GND), J102.A12 (GND), J102.B1 (GND), J102.B12 (GND), J102.S1 (SHIELD), J103.A1 (GND), J103.A12 (GND), J103.B1 (GND), J103.B12 (GND), J103.S1 (SHIELD), J104.2, J104.3, J104.5, R102.2, R109.1, R110.1, R114.2, R119.1, SW101.1, TP101.1, U101.4 (GND), U102.2 (GND), U103.1 (GND), U104.12 (GND), U104.33 (GNDPLL), U104.44 (GNDUTMI), U104.46 (JTAGSEL), U104.54 (GNDBU), U104.58 (GND), U104.74 (GNDANA), U104.106 (GND), U104.126 (GND), U105.2 (GND), U106.3 (GND), U106.28 (UGND), U106.33 (GND), U107.3 (GND), U108.3 (GND), Y101.2, Y101.4, Y102.2, Y102.4, Y103.2, Y103.4
unnamed: C106.1, L101.1, R103.1, R104.2
unnamed: C108.1, R104.1
unnamed: C119.2, F102.2, FB102.2
unnamed: C130.1, L102.2, R111.2, R112.2
unnamed: C133.1, R112.1
unnamed: C141.1, L103.2, R117.2, R118.2
unnamed: C144.1, R118.1
unnamed: D101.2 (A), R120.1
unnamed: D102.2 (A), R122.1
unnamed: J103.A5 (CC1), R109.2
unnamed: J103.B5 (CC2), R110.2
unnamed: R106.1, U104.43 (DFSDM)
unnamed: R105.1, U104.42 (DFSDP)
unnamed: C125.1, U104.48 (XIN32), Y103.3
unnamed: C114.1, U104.36 (XIN), Y102.3
unnamed: C127.1, U104.49 (XOUT32), Y103.1
unnamed: C121.1, U104.35 (XOUT), Y102.1
unnamed: C122.2, F101.2, FB101.1, U105.5 (VBUS)
unnamed: R113.1, U106.26 (PC4)

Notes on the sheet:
These should be as close to the MCU as possible.
ATMEGA16U2
N.C. Internal Pullup



Board: 2 copper layers, 102 parts (38 on the bottom side), 66 nets.

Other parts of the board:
J103#2: SODIMM DDR4 EDGE; SODIMM_DDR4_EDGE

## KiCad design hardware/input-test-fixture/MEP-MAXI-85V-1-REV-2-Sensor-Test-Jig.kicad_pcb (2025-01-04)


Board: 2 copper layers, 135.0 x 43.5 mm, 19 parts (0 on the bottom side), 17 nets.

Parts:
H101, H102, H103, H104: MountingHole_Pad; MountingHole_3.2mm_M3_Pad_Via
J101: Conn_02x10_Odd_Even; IDC-Header_2x10_P2.54mm_Vertical
J102, J103: Screw_Terminal_01x05; TerminalBlock_TE_282834-5_1x05_P2.54mm_Horizontal
J104, J105, J106, J107, J108, J109, J111, J112, J113: Screw_Terminal_01x03; TerminalBlock_TE_282834-3_1x03_P2.54mm_Horizontal
J110, J114: Screw_Terminal_01x02; TerminalBlock_TE_282834-2_1x02_P2.54mm_Horizontal
J115: Barrel_Jack_MountingPin; BarrelJack_Wuerth_6941xx301002

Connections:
24VRAW: J101.6, J102.1, J103.1, J104.1, J105.1, J106.1, J107.1, J108.1, J109.1, J111.1, J112.1, J113.1, J115.1
/AUTO_BUTTON: J101.17, J114.1
/ENCODER_BEND_RESET: J101.4, J103.3
/ENCODER_BEND_SET: J101.3, J103.2
/ENCODER_FEED_RESET: J101.2, J102.3
/ENCODER_FEED_SET: J101.1, J102.2
/PROXIMITY_HEAD_CCW: J101.16, J113.2
/PROXIMITY_HEAD_CW: J101.15, J112.2
/PROXIMITY_HEAD_IN: J101.8, J105.2
/PROXIMITY_HEAD_LIM: J101.14, J111.2
/PROXIMITY_HEAD_OUT: J101.7, J104.2
/PROXIMITY_SHEAR_CUT: J101.10, J107.2
/PROXIMITY_SHEAR_HOME: J101.9, J106.2
/PROXIMITY_TOOL_IN: J101.11, J108.2
/PROXIMITY_TOOL_OUT: J101.12, J109.2
/SHEAR_BUTTON: J101.13, J110.1
GND: H101.1, H102.1, H103.1, H104.1, J101.5, J102.4, J103.4, J104.3, J105.3, J106.3, J107.3, J108.3, J109.3, J110.2, J111.3, J112.3, J113.3, J114.2, J115.2, J115.3 (MountPin)

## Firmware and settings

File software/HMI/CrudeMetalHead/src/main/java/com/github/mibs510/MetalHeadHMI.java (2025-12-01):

package com.github.mibs510;

import java.awt.event.*;

import com.formdev.flatlaf.themes.FlatMacDarkLaf;
import com.intellij.uiDesigner.core.*;

import javax.swing.*;
import java.awt.*;
import java.io.*;
import java.text.SimpleDateFormat;
import java.time.LocalDateTime;
import java.time.format.DateTimeFormatter;

public class MetalHeadHMI extends JFrame {
    private final AsyncTCPClient tcpClient;
    private final DateTimeFormatter dateTimeFormatter = DateTimeFormatter.ofPattern("MM/dd/yyyy HH:mm:ss.SSS");

    public MetalHeadHMI() throws IOException {
        tcpClient = new AsyncTCPClient(this::onMessageReceived, this::updateUiComponents);

        FlatMacDarkLaf.setup();
        initComponents();
        // Center on screen
        hmiFrame.setLocationRelativeTo(null);
        // Show the GUI
        hmiFrame.setVisible(true);
        // If we click on the X on the top right, kill the process
        hmiFrame.setDefaultCloseOperation(JFrame.EXIT_ON_CLOSE);
        // Pad the size of the frame (hmiFrame) to accommodate the text/labels within
        // hmiFrame.pack();

        // Connect to server
        tcpClient.connect("192.168.1.36", 3682);
    }

    // Callback method to update the GUI from a background thread
    private void onMessageReceived(String message) {
        String formattedDateTime = LocalDateTime.now().format(dateTimeFormatter);
        final String msg = ("[" + formattedDateTime + "] " +
                message + "\n").replaceAll("(\\r?\\n)+", "\n");
        EventQueue.invokeLater(() -> debugTextArea.append(msg));
    }

    private void updateUiComponents(HmiServerMsgProto.HmiServerMsg hmiClientMsg) {
        // Everything below only needs to be set once at the start of the program.
        firmwareVersionValueLabel.setText(String.format("%d.%d.%d",
                hmiClientMsg.getHmiClientMsg().getMajorVersion(),
                hmiClientMsg.getHmiClientMsg().getMinorVersion(),
                hmiClientMsg.getHmiClientMsg().getPatchVersion()));

        bootCountValueLabel.setText(String.format("%d", hmiClientMsg.getHmiClientMsg().getBootCount()));

        StringBuilder serialNumber = new StringBuilder();
        for (int i = 0; i < hmiClientMsg.getHmiClientMsg().getSerialNumber().size(); i++) {
            serialNumber.append(hmiClientMsg.getHmiClientMsg().getSerialNumber().byteAt(i) & 0xFF);
        }
        serialNumberValueLabel.setText(serialNumber.toString());

        StringBuilder macAddress = new StringBuilder();
        for (int i = 0; i < hmiClientMsg.getHmiClientMsg().getMacAddress().size(); i++) {
            macAddress.append(String.format("%02X", hmiClientMsg.getHmiClientMsg().getMacAddress().byteAt(i) & 0xFF));
            if (i < hmiClientMsg.getHmiClientMsg().getMacAddress().size() - 1) {
                macAddress.append(":");
            }
        }
        macAddressValueLabel.setText(macAddress.toString());

        StringBuilder ipAddress = new StringBuilder();
        for (int i = 0; i < hmiClientMsg.getHmiClientMsg().getIpAddress().size(); i++) {
            ipAddress.append(hmiClientMsg.getHmiClientMsg().getIpAddress().byteAt(i) & 0xFF);
            if (i < hmiClientMsg.getHmiClientMsg().getIpAddress().size() - 1) {
                ipAddress.append(".");
            }
        }
        ipAddressValueLabel.setText(ipAddress.toString());

        StringBuilder subnetMask = new StringBuilder();
        for (int i = 0; i < hmiClientMsg.getHmiClientMsg().getSubnetMask().size(); i++) {
            subnetMask.append(hmiClientMsg.getHmiClientMsg().getSubnetMask().byteAt(i) & 0xFF);
            if (i < hmiClientMsg.getHmiClientMsg().getSubnetMask().size() - 1) {
                subnetMask.append(".");
            }
        }
        subnetMaskValueLabel.setText(subnetMask.toString());

        portValueLabel.setText(String.format("%d", hmiClientMsg.getHmiClientMsg().getPort()));

        StringBuilder hmiIpAddress = new StringBuilder();
        for (int i = 0; i < hmiClientMsg.getHmiClientMsg().getHmiIpAddress().size(); i++) {
            hmiIpAddress.append(hmiClientMsg.getHmiClientMsg().getHmiIpAddress().byteAt(i) & 0xFF);
            if (i < hmiClientMsg.getHmiClientMsg().getHmiIpAddress().size() - 1) {
                hmiIpAddress.append(".");
            }
        }
        hmiIpAddressValueLabel.setText(hmiIpAddress.toString());

        hmiPortValueLabel.setText(String.format("%d", hmiClientMsg.getHmiClientMsg().getHmiPort()));

        solenoidShearCutCheckBox.setSelected(hmiClientMsg.getHmiClientMsg().getShearCut());
        solenoidShearHomeCheckBox.setSelected(hmiClientMsg.getHmiClientMsg().getShearHome());
        solenoidToolOutCheckBox.setSelected(hmiClientMsg.getHmiClientMsg().getToolOut());
        solenoidToolInCheckBox.setSelected(hmiClientMsg.getHmiClientMsg().getToolIn());
        solenoidFeedForwardCheckBox.setSelected(hmiClientMsg.getHmiClientMsg().getFeedForward());
        solenoidFeedReverseCheckBox.setSelected(hmiClientMsg.getHmiClientMsg().getFeedReverse());
        solenoidHeadCwCheckBox.setSelected(hmiClientMsg.getHmiClientMsg().getHeadCw());
        solenoidHeadCcwCheckBox.setSelected(hmiClientMsg.getHmiClientMsg().getHeadCcw());
        solenoidHeadOutCheckBox.setSelected(hmiClientMsg.getHmiClientMsg().getHeadOut());
        solenoidHeadInCheckBox.setSelected(hmiClientMsg.getHmiClientMsg().getHeadIn());
        encoderFeedSetCheckBox.setSelected(hmiClientMsg.getHmiClientMsg().getEncoderFeedSet());
        encoderFeedResetCheckBox.setSelected(hmiClientMsg.getHmiClientMsg().getEncoderFeedReset());
        encoderBendSetCheckBox.setSelected(hmiClientMsg.getHmiClientMsg().getEncoderBendSet());
        encoderBendResetCheckBox.setSelected(hmiClientMsg.getHmiClientMsg().getEncoderBendReset());
        proximityHeadOutCheckBox.setSelected(hmiClientMsg.getHmiClientMsg().getProximityHeadOut());
        proximityHeadInCheckBox.setSelected(hmiClientMsg.getHmiClientMsg().getProximityHeadIn());
        proximityShearHomeCheckBox.setSelected(hmiClientMsg.getHmiClientMsg().getProximityShearHome());
        proximityShearCutCheckBox.setSelected(hmiClientMsg.getHmiClientMsg().getProximityShearCut());
        proximityToolInCheckBox.setSelected(hmiClientMsg.getHmiClientMsg().getProximityToolIn());
        proximityToolOutCheckbox.setSelected(hmiClientMsg.getHmiClientMsg().getProximityToolOut());
        buttonShearCheckBox.setSelected(hmiClientMsg.getHmiClientMsg().getShearButton());
        proximityHeadLimitCheckBox.setSelected(hmiClientMsg.getHmiClientMsg().getProximityHeadLimit());
        proximityHeadCwCheckBox.setSelected(hmiClientMsg.getHmiClientMsg().getProximityHeadCw());
        proximityHeadCcwCheckBox.setSelected(hmiClientMsg.getHmiClientMsg().getProximityHeadCcw());
        buttonAutoCheckBox.setSelected(hmiClientMsg.getHmiClientMsg().getAutoButton());
        buttonEstopCheckBox.setSelected(hmiClientMsg.getHmiClientMsg().getEStop());
        fuseCheckBox.setSelected(hmiClientMsg.getHmiClientMsg().getFuse());
        twentyFourVRawCheckBox.setSelected(hmiClientMsg.getHmiClientMsg().getVRawTwentyFour());
        auxTwentyFourVCheckBox.setSelected(hmiClientMsg.getHmiClientMsg().getAuxTwentyFourV());
        encoderFeedCountValueLabel.setText(String.format("%d", hmiClientMsg.getHmiClientMsg().getEncoderFeedCount()));
        encoderBendCountValueLabel.setText(String.format("%d", hmiClientMsg.getHmiClientMsg().getEncoderBendCount()));
        twentyFourVRawVoltValueLabel.setText(Float.toString(
                hmiClientMsg.getHmiClientMsg().getTwentyFourVrawBusVoltage()));
        twentyFourVRawCurrentValueLabel.setText(Float.toString(
                hmiClientMsg.getHmiClientMsg().getTwentyFourVrawBusCurrent()));
        aux24vVoltValueLabel.setText(Float.toString(hmiClientMsg.getHmiClientMsg().getAuxTwentyFourVBusVoltage()));
        aux24vCurrentValueLabel.setText(Float.toString(hmiClientMsg.getHmiClientMsg().getAuxTwentyFourVBusCurrent()));
        twelvevVoltValueLabel.setText(Float.toString(hmiClientMsg.getHmiClientMsg().getTwelveVBusVoltage()));
        twelvevCurrentValueLabel.setText(Float.toString(hmiClientMsg.getHmiClientMsg().getTwelveVBusCurrent()));
        fivevVoltValueLabel.setText(Float.toString(hmiClientMsg.getHmiClientMsg().getFiveVBusVoltage()));
        fivevCurrentValueLabel.setText(Float.toString(hmiClientMsg.getHmiClientMsg().getFiveVBusCurrent()));
        threevThreeVoltValueLabel.setText(Float.toString(hmiClientMsg.getHmiClientMsg().getThreeVThreeVBusVoltage()));
        threevThreeCurrentValueLabel.setText(
                Float.toString(hmiClientMsg.getHmiClientMsg().getThreeVThreeVBusCurrent()));
        fGndVoltValueLabel.setText(Float.toString(hmiClientMsg.getHmiClientMsg().getFGndBusVoltage()));
        fGndCurrentValueLabel.setText(Float.toString(hmiClientMsg.getHmiClientMsg().getFGndBusCurrent()));
        stateValueLabel.setText(hmiClientMsg.getHmiClientMsg().getState().toString());
        actionValueLabel.setText(hmiClientMsg.getHmiClientMsg().getAction().toString());
        // Right size the main JFrame, or else the Misc column gets cutoff
        hmiFrame.pack();
    }

    private void onStatusUpdate(String status) {
        EventQueue.invokeLater(() -> debugTextArea.append("Status: " + status + "\n"));
    }

    public static void main(String[] args) {
        // Start the Swing application on the EDT
        EventQueue.invokeLater(() -> {
            try {
                new MetalHeadHMI();
            } catch (IOException e) {
                e.printStackTrace();
            }
        });
    }

    private void openMakeShapeWindow(ActionEvent e) {
        // Make the Dialog window visible in the center of the parent Frame (hmiFrame)
        makeShapeJDialog.setLocationRelativeTo(this.hmiFrame);
        // This makes the parent Frame (hmiFrame) inaccessible while this is open
        makeShapeJDialog.setModalityType(Dialog.ModalityType.APPLICATION_MODAL);
        makeShapeJDialog.setVisible(true);
    }

    private void manualActionsButtonClicked(ActionEvent e) {
        // Make the Dialog window visible in the center of the parent Frame (hmiFrame)
        manualActionsJDialog.setLocationRelativeTo(this.hmiFrame);
        // This makes the parent Frame (hmiFrame) inaccessible while this is open
        manualActionsJDialog.setModalityType(Dialog.ModalityType.APPLICATION_MODAL);
        manualActionsJDialog.setVisible(true);
    }

    private void headOut(ActionEvent e) {
        HmiClientMsgProto.HmiClientMessage msg = HmiClientMsgProto.HmiClientMessage.newBuilder()
                .setHmiClientActionValue(HmiClientMsgProto.HmiClientMessage.HMICLIENTACTION_FIELD_NUMBER)
                .setHmiClientAction(HmiClientMsgProto.HmiClientAction.ACTION_HEAD_OUT)
                .build();
        tcpClient.sendMessage(msg);
    }

	public void initComponents() {
		// JFormDesigner - Component initialization - DO NOT MODIFY  //GEN-BEGIN:initComponents  @formatter:off
        // Generated using JFormDesigner Educational license - Connor McMillan
        hmiFrame = new JFrame();
        statusIndicatorsLabelPanel = new JPanel();
        statusIndicatorsLabel = new JLabel();
        everythingelsePanel = new JPanel();
        solenoidsLabel = new JLabel();
        encodersLabel = new JLabel();
        proximitySensorLabel = new JLabel();
        buttonsLabel = new JLabel();
        currentMonitorLabel = new JLabel();
        miscLabel = new JLabel();
        solenoidsPanel = new JPanel();
        solenoidShearCutCheckBox = new JCheckBox();
        solenoidShearHomeCheckBox = new JCheckBox();
        solenoidToolOutCheckBox = new JCheckBox();
        solenoidToolInCheckBox = new JCheckBox();
        solenoidFeedForwardCheckBox = new JCheckBox();
        solenoidFeedReverseCheckBox = new JCheckBox();
        solenoidHeadCwCheckBox = new JCheckBox();
        solenoidHeadCcwCheckBox = new JCheckBox();
        solenoidHeadOutCheckBox = new JCheckBox();
        solenoidHeadInCheckBox = new JCheckBox();
        encodersPanel = new JPanel();
        encoderFeedSetCheckBox = new JCheckBox();
        encoderFeedResetCheckBox = new JCheckBox();
        encoderBendSetCheckBox = new JCheckBox();
        encoderBendResetCheckBox = new JCheckBox();
        encoderFeedCountLabel = new JLabel();
        encoderFeedCountValueLabel = new JLabel();
        encoderBendCountLabel = new JLabel();
        encoderBendCountValueLabel = new JLabel();
        proximitySensorsPanel = new JPanel();
        proximityHeadOutCheckBox = new JCheckBox();
        proximityHeadInCheckBox = new JCheckBox();
        proximityShearHomeCheckBox = new JCheckBox();
        proximityShearCutCheckBox = new JCheckBox();
        proximityToolInCheckBox = new JCheckBox();
        proximityToolOutCheckbox = new JCheckBox();
        proximityHeadLimitCheckBox = new JCheckBox();
        proximityHeadCwCheckBox = new JCheckBox();
        proximityHeadCcwCheckBox = new JCheckBox();
        buttonsPanel = new JPanel();
        buttonShearCheckBox = new JCheckBox();
        buttonAutoCheckBox = new JCheckBox();
        buttonEstopCheckBox = new JCheckBox();
        currentMonitorsPanel = new JPanel();
        twentyFourVRawVoltLabel = new JLabel();
        twentyFourVRawVoltValueLabel = new JLabel();
        twentyFourVRawCurrentLabel = new JLabel();
        twentyFourVRawCurrentValueLabel = new JLabel();
        aux24vVoltLabel = new JLabel();
        aux24vVoltValueLabel = new JLabel();
        aux24vCurrentLabel = new JLabel();
        aux24vCurrentValueLabel = new JLabel();
        twelvevVoltLabel = new JLabel();
        twelvevVoltValueLabel = new JLabel();
        twelvevCurrentLabel = new JLabel();
        twelvevCurrentValueLabel = new JLabel();
        fivevVoltLabel = new JLabel();
        fivevVoltValueLabel = new JLabel();
        fivevCurrentLabel = new JLabel();
        fivevCurrentValueLabel = new JLabel();
        threevThreeVoltLabel = new JLabel();
        threevThreeVoltValueLabel = new JLabel();
        threevThreeCurrentLabel = new JLabel();
        threevThreeCurrentValueLabel = new JLabel();
        fGndVoltLabel = new JLabel();
        fGndVoltValueLabel = new JLabel();
        fGndCurrentLabel = new JLabel();
        fGndCurrentValueLabel = new JLabel();
        miscPanel = new JPanel();
        fuseCheckBox = new JCheckBox();
        twentyFourVRawCheckBox = new JCheckBox();
        auxTwentyFourVCheckBox = new JCheckBox();
        interfaceBoardLabel = new JLabel();
        firmwareVersionLabel = new JLabel();
        firmwareVersionValueLabel = new JLabel();
        bootCountLabel = new JLabel();
        bootCountValueLabel = new JLabel();
        serialNumberLabel = new JLabel();
        serialNumberValueLabel = new JLabel();
        macAddressLabel = new JLabel();
        macAddressValueLabel = new JLabel();
        ipAddressLabel = new JLabel();
        ipAddressValueLabel = new JLabel();
        subnetMaskLabel = new JLabel();
        subnetMaskValueLabel = new JLabel();
        portLabel = new JLabel();
        portValueLabel = new JLabel();
        hmiIpAddressLabel = new JLabel();
        hmiIpAddressValueLabel = new JLabel();
        hmiPortLabel = new JLabel();
        hmiPortValueLabel = new JLabel();
        statePanel = new JPanel();
        stateLabel = new JLabel();
        stateValueLabel = new JLabel();
        actionPanel = new JPanel();
        actionLabel = new JLabel();
        actionValueLabel = new JLabel();
        makeShapeButton = new JButton();
        manualActionsButton = new JButton();
        debugLogLabel = new JLabel();
        debugLogScrollPane = new JScrollPane();
        debugTextArea = new JTextArea();
        makeShapeJDialog = new JDialog();
        makeShapePanel = new JPanel();
        makeShapeScrollPane = new JScrollPane();
        makeShapeRowsPanel = new JPanel();
        lengthLabel = new JLabel();
        lengthTextField = new JTextField();
        bendDegreeLabel = new JLabel();
        bendDegreeTextField = new JTextField();
        directionLabel = new JLabel();
        directionComboBox = new JComboBox();
        lengthCompLabel = new JLabel();
        lengthCompTextField = new JTextField();
        bendCompLabel = new JLabel();
        bendCompTextField = new JTextField();
        addLineSendPanel = new JPanel();
        addLineButton = new JButton();
        sendButton = new JButton();
        manualActionsJDialog = new JDialog();
        manualActionsPanel = new JPanel();
        headOutButton = new JButton();
        headInButton = new JButton();
        shearHomeButton = new JButton();
        shearCutButton = new JButton();
        toolInButton = new JButton();
        toolOutButton = new JButton();
        headLimitButton = new JButton();
        headCwButton = new JButton();
        headCcwButton = new JButton();
        feedForwardButton = new JButton();
        feedReverseButton = new JButton();
        eStopButton = new JButton();

        //======== hmiFrame ========
        {
            hmiFrame.setTitle("MetalHead HMI - Crude Edition");
            hmiFrame.setIconImage(new ImageIcon(getClass().getResource("/MH-W-64.png")).getImage());
            var hmiFrameContentPane = hmiFrame.getContentPane();
            hmiFrameContentPane.setLayout(new GridLayoutManager(5, 3, new Insets(10, 10, 10, 10), -1, -1));

            //======== statusIndicatorsLabelPanel ========
            {
                statusIndicatorsLabelPanel.setLayout(new GridLayoutManager(3, 3, new Insets(0, 0, 0, 0), -1, -1));

                //---- statusIndicatorsLabel ----
                statusIndicatorsLabel.setText("Status Indicators");
                statusIndicatorsLabel.setFont(new Font("Inter", Font.BOLD, 26));
                statusIndicatorsLabelPanel.add(statusIndicatorsLabel, new GridConstraints(1, 1, 1, 1,
                    GridConstraints.ANCHOR_CENTER, GridConstraints.FILL_BOTH,
                    GridConstraints.SIZEPOLICY_CAN_SHRINK | GridConstraints.SIZEPOLICY_CAN_GROW,
                    GridConstraints.SIZEPOLICY_CAN_SHRINK | GridConstraints.SIZEPOLICY_CAN_GROW,
                    null, null, null));
            }
            hmiFrameContentPane.add(statusIndicatorsLabelPanel, new GridConstraints(0, 1, 1, 1,
                GridConstraints.ANCHOR_CENTER, GridConstraints.FILL_NONE,
                GridConstraints.SIZEPOLICY_CAN_SHRINK | GridConstraints.SIZEPOLICY_CAN_GROW,
                GridConstraints.SIZEPOLICY_CAN_SHRINK | GridConstraints.SIZEPOLICY_CAN_GROW,
                null, null, null));

            //======== everythingelsePanel ========
            {
                everythingelsePanel.setLayout(new GridLayoutManager(5, 6, new Insets(10, 10, 10, 10), -1, -1));

                //---- solenoidsLabel ----
                solenoidsLabel.setText("Solenoids");
                solenoidsLabel.setFont(new Font("Inter", Font.BOLD, 20));
                everythingelsePanel.add(solenoidsLabel, new GridConstraints(0, 0, 1, 1,
                    GridConstraints.ANCHOR_CENTER, GridConstraints.FILL_NONE,
                    GridConstraints.SIZEPOLICY_CAN_SHRINK | GridConstraints.SIZEPOLICY_CAN_GROW,
                    GridConstraints.SIZEPOLICY_CAN_SHRINK | GridConstraints.SIZEPOLICY_CAN_GROW,
                    null, null, null));

                //---- encodersLabel ----
                encodersLabel.setText("Encoders");
                encodersLabel.setFont(new Font("Inter", Font.BOLD, 20));
                everythingelsePanel.add(encodersLabel, new GridConstraints(0, 1, 1, 1,
                    GridConstraints.ANCHOR_CENTER, GridConstraints.FILL_NONE,
                    GridConstraints.SIZEPOLICY_CAN_SHRINK | GridConstraints.SIZEPOLICY_CAN_GROW,
                    GridConstraints.SIZEPOLICY_CAN_SHRINK | GridConstraints.SIZEPOLICY_CAN_GROW,
                    null, null, null));

                //---- proximitySensorLabel ----
                proximitySensorLabel.setText("Proximity Sensors");
                proximitySensorLabel.setFont(new Font("Inter", Font.BOLD, 20));
                everythingelsePanel.add(proximitySensorLabel, new GridConstraints(0, 2, 1, 1,
                    GridConstraints.ANCHOR_CENTER, GridConstraints.FILL_NONE,
                    GridConstraints.SIZEPOLICY_CAN_SHRINK | GridConstraints.SIZEPOLICY_CAN_GROW,
                    GridConstraints.SIZEPOLICY_CAN_SHRINK | GridConstraints.SIZEPOLICY_CAN_GROW,
                    null, null, null));

                //---- buttonsLabel ----
                buttonsLabel.setText("Buttons");
                buttonsLabel.setFont(new Font("Inter", Font.BOLD, 20));
                everythingelsePanel.add(buttonsLabel, new GridConstraints(0, 3, 1, 1,
                    GridConstraints.ANCHOR_CENTER, GridConstraints.FILL_NONE,
                    GridConstraints.SIZEPOLICY_CAN_SHRINK | GridConstraints.SIZEPOLICY_CAN_GROW,
                    GridConstraints.SIZEPOLICY_CAN_SHRINK | GridConstraints.SIZEPOLICY_CAN_GROW,
                    null, null, null));

                //---- currentMonitorLabel ----
                currentMonitorLabel.setText("Current Monitors");
                currentMonitorLabel.setFont(new Font("Inter", Font.BOLD, 20));
                everythingelsePanel.add(currentMonitorLabel, new GridConstraints(0, 4, 1, 1,
                    GridConstraints.ANCHOR_CENTER, GridConstraints.FILL_NONE,
                    GridConstraints.SIZEPOLICY_CAN_SHRINK | GridConstraints.SIZEPOLICY_CAN_GROW,
                    GridConstraints.SIZEPOLICY_CAN_SHRINK | GridConstraints.SIZEPOLICY_CAN_GROW,
                    null, null, null));
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

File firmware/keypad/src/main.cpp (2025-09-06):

#include <Arduino.h>
#include <Wire.h>
#include <PCF8575.h>
#include <pins.h>
#include <keys.h>

uint8_t pi02wI2cAddr = 100;
PCF8575 PCF1(0x20);
PCF8575 PCF2(0x21);
uint16_t pcf1;
uint16_t pcf2;

/*
 *
 * INTERRUPT ROUTINE + FLAG
 *
 */
volatile bool flag = false;
volatile bool repeatFlag = false;

void pcf_irq(){
  flag = true;
}

void repeat_irq() {
  repeatFlag = true;
}

void send(const char key[]) {
  Serial.println(key);
  Wire.beginTransmission(pi02wI2cAddr);
  Wire.write(key);
  Wire.endTransmission();
}

void setup() {
  // while(!Serial);
  Serial.begin(115200);

  // Let's establish ourselves as
  Wire.begin();

  // Let's initiate the conversation on the i2c bus
  PCF1.begin();
  PCF2.begin();

  // Set the mode for the interrupt pins
  pinMode(PCF8575_INT, INPUT);
  pinMode(REPEATER_INT, INPUT);

  // Tell the uC which function to execute when interrupted
  attachInterrupt(digitalPinToInterrupt(PCF8575_INT), pcf_irq, RISING);
  attachInterrupt(digitalPinToInterrupt(REPEATER_INT), repeat_irq, RISING);
}

void loop() {
  // Something happened. Let's find out.
  if (flag || repeatFlag) {
    // Reset the flag
    flag = false;
    // Read the status of which keys were (de)pressed from both GPIO expanders
    pcf1 = PCF1.read16();
    pcf2 = PCF2.read16();

    // Someone (de)pressed a key.
    if (pcf1 != 0 || pcf2 != 0) {
      if (pcf1 & DISP && !stateDisplay) {
        stateDisplay = true;
        send("DISPLAY");
      }
      if (pcf1 & COMP && !stateComp) {
        stateComp = true;
        send("COMP");
      }
      if (pcf1 & INFEED && !stateInfeed) {
        stateInfeed = true;
        send("INFEED");
      }
      if (pcf1 & HEAD_POS && !stateHeadPos) {
        stateHeadPos = true;
        send("HEAD_POS");
      }
      if (pcf1 & FORM_TOOL_IN && !stateFormToolIn) {
        stateFormToolIn = true;
        send("FORM_TOOL_IN");
      }
      if (pcf1 & SHEAR && !stateShear) {
        stateShear = true;
        send("SHEAR");
      }
      if (pcf1 & PAUSE && !statePause) {
        statePause = true;
        send("PAUSE");
      }
      if (pcf1 & RUN && !stateRun) {
        stateRun = true;
        send("RUN");
      }
      if (pcf1 & UP && (!stateUp || repeatFlag)) {
        stateUp = true;
        send("UP");
      }
      if (pcf1 & ENTER && !stateEnter) {
        stateEnter = true;
        send("ENTER");
      }
      if (pcf1 & ONE && (!stateOne || repeatFlag)) {
        stateOne = true;
        send("ONE");
      }
      if (pcf1 & TWO && (!stateTwo || repeatFlag)) {
        stateTwo = true;
        send("TWO");
      }
      if (pcf1 & THREE && (!stateThree || repeatFlag)) {
        stateThree = true;
        send("THREE");
      }
      if (pcf1 & PLUS && (!statePlus || repeatFlag)) {
        statePlus = true;
        send("PLUS");
      }
      if (pcf1 & LEFT && (!stateLeft || repeatFlag)){
        stateLeft = true;
        send("LEFT");
      }
      if (pcf1 & MENU && !stateMenu) {
        stateMenu = true;
        send("MENU");
      }
      // PCF2
      if (pcf2 & RIGHT && (!stateRight || repeatFlag)) {
        stateRight = true;
        send("RIGHT");
      }
      if (pcf2 & FOUR && (!stateFour || repeatFlag)) {
        stateFour = true;
        send("FOUR");
      }
      if (pcf2 & FIVE && (!stateFive || repeatFlag)) {
        stateFive = true;
        send("FIVE");
      }
      if (pcf2 & SIX && (!stateSix || repeatFlag)) {
        stateSix = true;
        send("SIX");
      }
      if (pcf2 & MINUS && (!stateMinus || repeatFlag)) {
        stateMinus = true;
        send("MINUS");
      }
      if (pcf2 & MEMORY && (!stateMemory || repeatFlag)) {
        stateMemory = true;
        send("MEMORY");
      }
      if (pcf2 & DOWN && (!stateDown || repeatFlag)) {
        stateDown = true;
        send("DOWN");
      }
      if (pcf2 & DECIMAL && !stateDecimal) {
        stateDecimal = true;
        send("DECIMAL");
      }
      if (pcf2 & SEVEN && (!stateSeven || repeatFlag)) {
        stateSeven = true;
        send("SEVEN");
      }
      if (pcf2 & EIGHT && (!stateEight || repeatFlag)) {
        stateEight = true;
        send("EIGHT");
      }
      if (pcf2 & NINE && (!stateNine || repeatFlag)) {
        stateNine = true;
        send("NINE");
      }
      if (pcf2 & ZERO && (!stateZero || repeatFlag)) {
        stateZero = true;
        send("ZERO");
      }
    }

    // Update flags and bits
    updatePCFStates(pcf1, pcf2);
    repeatFlag = false;
  }
}

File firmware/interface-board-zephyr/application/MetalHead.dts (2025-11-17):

/ {
	aliases {
		eeprom-0 = &at24_eeprom_0;
	};

	// Solenoids
	shear_cut: shear_cut {
		compatible = "gpio";
		gpios = <&piob 26 0>;
		label = "SHEAR_CUT";
	};
	shear_home: shear_home {
		compatible = "gpio";
		gpios = <&pioa 14 0>;
		label = "SHEAR_HOME";
	};
	tool_out: tool_out {
		compatible = "gpio";
		gpios = <&pioa 15 0>;
		label = "TOOL_OUT";
	};
	tool_in: tool_in {
		compatible = "gpio";
		gpios = <&piod 0 0>;
		label = "TOOL_IN";
	};
	feed_forward: feed_forward {
		compatible = "gpio";
		gpios = <&piod 1 0>;
		label = "FEED_FORWARD";
	};
	feed_reverse: feed_reverse {
		compatible = "gpio";
		gpios = <&piod 2 0>;
		label = "FEED_REVERSE";
	};
	head_cw: head_cw {
		compatible = "gpio";
		gpios = <&piod 3 0>;
		label = "HEAD_CW";
	};
	head_ccw: head_ccw {
		compatible = "gpio";
		gpios = <&piod 6 0>;
		label = "HEAD_CCW";
	};
	head_out: head_out {
		compatible = "gpio";
		gpios = <&piod 9 0>;
		label = "HEAD_OUT";
	};
	head_in: head_in {
		compatible = "gpio";
		gpios = <&pioa 7 0>;
		label = "HEAD_IN";
	};

	// Encoders
	encoder_feed_set: encoder_feed_set {
		compatible = "gpio";
		gpios = <&piod 10 0>;
		label = "ENCODER_FEED_SET";
	};
	encoder_feed_reset: encoder_feed_reset {
		compatible = "gpio";
		gpios = <&pioc 1 0>;
		label = "ENCODER_FEED_RESET";
	};
	encoder_bend_set: encoder_bend_set {
		compatible = "gpio";
		gpios = <&pioc 2 0>;
		label = "ENCODER_BEND_SET";
	};
	encoder_bend_reset: encoder_bend_reset {
		compatible = "gpio";
		gpios = <&pioc 3 0>;
		label = "ENCODER_BEND_RESET";
	};

	// Proximity sensors
	proximity_head_out: proximity_head_out {
		compatible = "gpio";
		gpios = <&pioc 4 0>;
		label = "PROXIMITY_HEAD_OUT";
	};
	proximity_head_in: proximity_head_in {
		compatible = "gpio";
		gpios = <&pioc 5 0>;
		label = "PROXIMITY_HEAD_IN";
	};
	proximity_shear_home: proximity_shear_home {
		compatible = "gpio";
		gpios = <&pioc 6 0>;
		label = "PROXIMITY_SHEAR_HOME";
	};
	proximity_shear_cut: proximity_shear_cut {
		compatible = "gpio";
		gpios = <&pioc 7 0>;
		label = "PROXIMITY_SHEAR_CUT";
	};
	proximity_tool_in: proximity_tool_in {
		compatible = "gpio";
		gpios = <&pioc 8 0>;
		label = "PROXIMITY_TOOL_IN";
	};
	proximity_tool_out: proximity_tool_out {
		compatible = "gpio";
		gpios = <&pioc 9 0>;
		label = "PROXIMITY_TOOL_OUT";
	};
	proximity_head_limit: proximity_head_limit {
		compatible = "gpio";
		gpios = <&pioa 20 0>;
		label = "PROXIMITY_HEAD_LIMIT";
	};
	proximity_head_cw: proximity_head_cw {
		compatible = "gpio";
		gpios = <&pioc 19 0>;
		label = "PROXIMITY_HEAD_CW";
	};
	proximity_head_ccw: proximity_head_ccw {
		compatible = "gpio";
		gpios = <&pioc 18 0>;
		label = "PROXIMITY_HEAD_CCW";
	};

	// Buttons
	shear_button: shear_button {
		compatible = "gpio";
		gpios = <&pioa 19 0>;
		label = "SHEAR_BUTTON";
	};
	auto_button: auto_button {
		compatible = "gpio";
		gpios = <&pioc 17 0>;
		label = "AUTO_BUTTON";
	};

	// Auxillary
	estop: estop {
		compatible = "gpio";
		gpios = <&pioc 16 1>; // The 1 will invert the active logic
		label = "ESTOP";
	};
	fuse: fuse {
		compatible = "gpio";
		gpios = <&pioc 15 1>; // The 1 will invert the active logic
		label = "FUSE";
	};

	// Power
	vraw24: vraw24 {
		compatible = "gpio";
		gpios = <&pioc 14 0>;
		label = "24VRAW";
	};
	aux24v: aux24v {
		compatible = "gpio";
		gpios = <&pioc 13 0>;
		label = "AUX24V";
	};
};

&twi1 {
	status = "okay";
	clock-frequency = <I2C_BITRATE_FAST>;
	at24_eeprom_0: eeprom@50 {
		compatible = "atmel,at24";
		reg = <0x50>;
		size = <32768>;
		pagesize = <64>;
		address-width = <16>;
		timeout = <5>;
		label = "EEPROM";
	};
	ina226_0: ina226@40 {
		compatible = "ti,ina226";
		reg = <0x40>; // I2C address
		label = "FUSED_GND";
		avg-count = <256>;
		rshunt-micro-ohms = <2000>; // Example: 2 mOhm shunt
		current-lsb-microamps = <457>;  // Example: 457 uA/LSB (15A)
		// Other configurations like bus-voltage-resistor etc.
	};
	ina3221_0: ina3221@41 {
		compatible = "ti,ina3221";
		reg = <0x41>; // I2C address
		label = "TRI-VBUS";
		conv-time-shunt = <4>; // 1.1mS
		conv-time-bus = <4>; // 1.1mS
		avg-mode = <0>; // 1 sample
		enable-channel = <1 1 1>; // Channels 1-3
		shunt-resistors = <2 2 2>; // mOhms for channels 1-3
	};
};

&spi0 {
	w5500: w5500@0 {
		compatible = "wiznet,w5500";
		reg = <0>; // Chip select line
		spi-max-frequency = <8000000>; // Example frequency
		int-gpios = <&piod 7 GPIO_ACTIVE_LOW>; // Replace with your GPIO port and pin
		reset-gpios = <&pioc 25 GPIO_ACTIVE_LOW>; // Replace with your GPIO port and pin
	};
};

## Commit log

2024-12-28 Initiate Git LFS
    Track *.pdf files using Git LFS
2024-12-28 Initial commit
    Let's do this!
    [MEP-MAXI-85V-1-REV-2-Interface-Board.kicad_pcb, MEP-MAXI-85V-1-REV-2-Interface-Board.kicad_sch, arduino_due_io.kicad_sch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]
2025-01-04 X1 Release
    Released X1 revision for both the interface board and the input test fixture breakout board.
    [BOM-MEP-MAXI-85V-1-REV-2-Interface-Board.csv, BOM-MEP-MAXI-85V-1-REV-2-Sensor-Test-Jig.csv, Input Test Fixture v3.iges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]
2025-01-19 Input Test Fixture Rev X2
    [Input Test Fixture X2.step]
2025-01-19 Remove KiCAD lock files
    Removed some KiCAD lock files.
2025-01-29 Updated Drawings W H V S.pdf
    Updated Drawings W H V S.pdf to include the truth table for the bend & feed encoder multiplexer.
2025-02-11 Update README.md
    Updated README.md to include KeypadEvents forwarded from the HMI to the Interface Board when certain keys are pressed.
2025-02-19 Interface Board Test Sketch
    Sketch containing comments and code for testing the interface board.
2025-02-24 Interrupt Queue
    Added a queue to debug interrupts.
2025-03-09 SBC Carrier Board
    Started to design schematic for the SBC carrier board that will host the HMI application.
    [hmi-carrier-board.kicad_pcb, hmi-carrier-board.kicad_sch]
2025-03-09 Keypad Schematic
    Started to design the schematic for the keypad. Far from being a X1 rev release.
    [gpio_i2c_expanders.kicad_sch, keypad.kicad_pcb, keypad.kicad_sch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]
2025-05-04 Remove HMI Carrier Board
    The HMI SBC will be integrated (semi) into the interface board starting on rev X2.
    [hmi-carrier-board.kicad_pcb, hmi-carrier-board.kicad_sch]
2025-06-01 Housekeeping
    Removing large files from LFS.
    [MEP-MAXI-85V-1-REV-2-Interface-Board.step]
2025-06-01 Rev X1
    Finalized rev X1 of the keypad!
    [debounce.kicad_sch, gpio_i2c_expanders.kicad_sch, keypad.kicad_pcb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]
2025-06-01 Rev X2
    Finalized rev X2 of the interface board!
    Hopefully there are no major bugs!🤞
    [BOM-MEP-MAXI-85V-1-REV-2-Interface-Board.csv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]
2025-06-01 Update .gitignore
    Updated to exclude mp4 files and 85V Maintenance Schedule.pdf
2025-06-01 Updated .gitignore
    Yet another .gitignore update again!😞
2025-06-01 Create README.md
    Created a README.md for the video sub directory to list filenames and publicly accessible links for the videos. This is to switch from Github's paid LFS service.
2025-06-22 Revision X2!
    New and improved revision of the keypad! I fixed issues with the repeater and remote SBC power switch circuit (hopefully🤞). I also integrated the Arduino Nano onto the board (ATMEGA328).
    [debounce.kicad_sch, keypad.kicad_pcb, keypad.kicad_sch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]
2025-06-29 Initial firmware for keypad
    Some more minor implementations for the keypad to come. Are we still going to send the keystrokes via i2c?? And to what address?? Serial.println() will be good for now.
2025-09-06 Initial Arduino API
    Initial Arduino API based firmware for the interface board. This is just the starting point to something bigger.
2025-09-06 Keypad Firmware Updates
    Fixed attachInterrupts for the repeater, consolidated sending to serial into a subroutine (send(const char key[]))and added I2C transmission function.
    [main.cpp]
2025-09-06 Java StatusIndicators Client
    A very crud console client that connects to the interface board, receives a StatusIndicators data structure, and outputs it into the console.
2025-09-26 Rename to Arduino
    Renamed the current interface-board folder under firmware to add 'arduino' in effort to bring in the initial Zephyr RTOS code base.
2025-11-15 Remove old code
    Remove old Arduino code
2025-11-17 Async TCP Compatibility
    Reimplemented it to make it compatible with the interface board async TCP server. Fixed a lot of GUI issues and added a scrollable text debug log section.
    [MetalHeadHMI.java]
2025-12-01 Refactor threading and messaging headers
    Removed semaphores.h and added shape_processor_thread.h to improve thread management. Updated async_tcp_server.h, hmi_client_msg.proto, hmi_server_msg_t.proto, init_current_mon.h, init_net.h, interfa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
2025-12-01 Update protobuf usage and server message enums
    Updated proto file comments for correct protoc usage paths. Modified the State enum in HmiServerMsg.proto and corresponding generated code to add STATE_PROCESS_ACTION and shift enum values. Refactored generated Java code for compatibility with Protobuf Java 4.x, including changes to builder logic and field accessors. Minor comment update in MetalHeadHMI for window close behavior. Cleaned up unused code in AsyncTCPClient.
    [MetalHeadHMI.java]
